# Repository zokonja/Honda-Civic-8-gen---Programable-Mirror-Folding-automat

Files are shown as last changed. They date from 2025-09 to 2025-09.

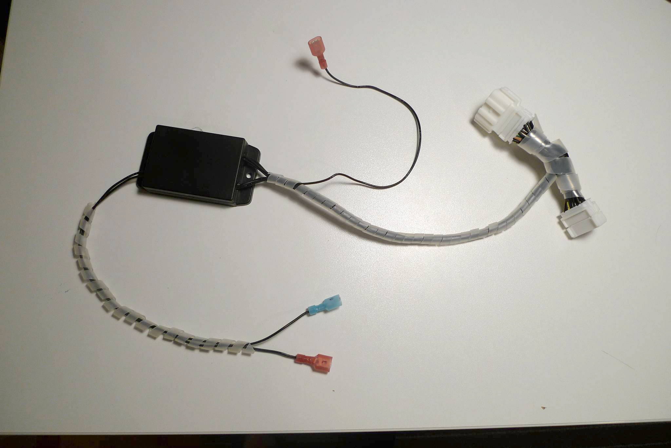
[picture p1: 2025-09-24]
Honda Civic 8 gen - Programable Mirror Folding automat/Pictures/P1070789.JPG

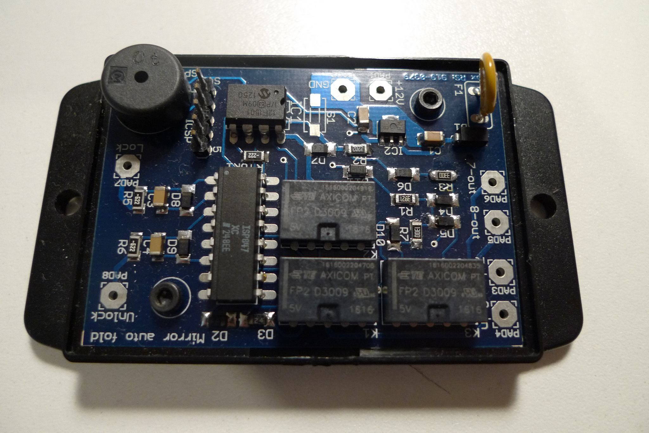
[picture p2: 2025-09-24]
Honda Civic 8 gen - Programable Mirror Folding automat/Pictures/P1070769.JPG

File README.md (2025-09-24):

Custom designed automat for Honda Civic 8gen for automatic mirrors fold/unfold.
Automat is programable and can be set to 5 different programs (behaviour actions).
Inside is complete device schematic (based on Microchip PIC 12F1501 micro) and firmware written in assembler and compiled HEX file for 12F1501.
Installation and demonstration video: https://youtu.be/eVyPs17ZJMc

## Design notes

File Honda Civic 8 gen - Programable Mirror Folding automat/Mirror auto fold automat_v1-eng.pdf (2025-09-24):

### Programable mirror folding automat (Civic 8th gen)

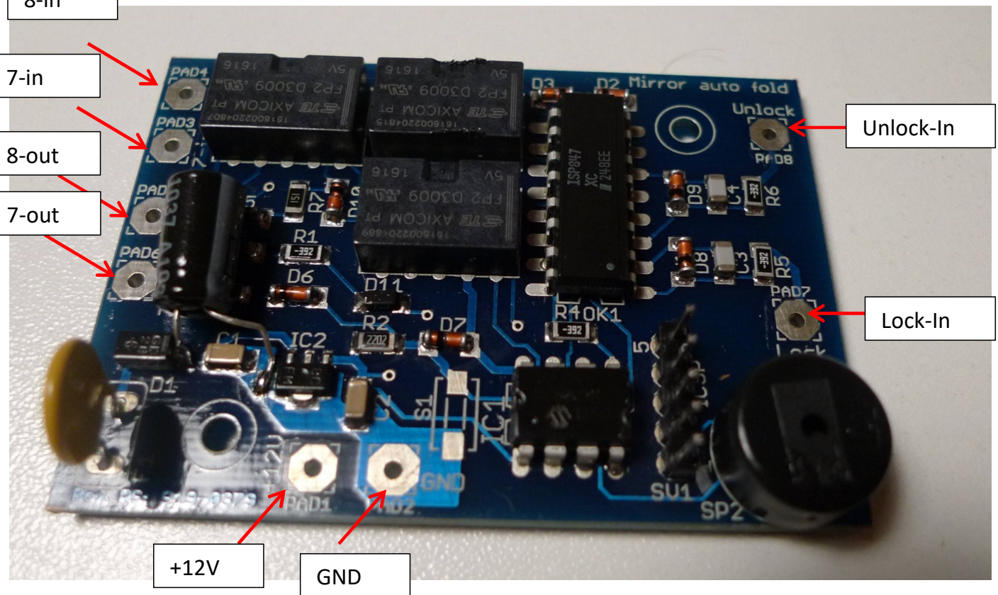
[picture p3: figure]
8-out; 7-out; GND; Unlock-In; Lock-In

Pin | Function | Connected to ...
GND | Ground (-) | Y connector
+12V | Power supply 12V (permanent) | 12V power supply on the window connector
8 - inch | Pin 8 from the female connector – signal from the mirror switch. If 12V appears at that input, it signals that the contact is ON. The same input detects whether the mirror switch is pressed. If the input is connected to ground (GND), the switch is pressed. | Y connector
7 - inch | Pin 7 from the female connector - signal from the mirror switch. If 12V appears at that input, it signals that the contact is ON. | Y connector
8 - out | Pin 8 from male connector, output to mirrors | Y connector
7 - out | Pin 7 from male connector, output to mirrors | Y connector
Lock-in | Lock signal input, 12V active | Central connector
Unlock - in | Unlock signal input, 12V active | Central connector

The Lock and Unlock signals are filtered from interference in the controller's SW, 80 ms debouncing time means that the signal must be active for a minimum of 80 ms without interruption in order to be processed.

The "8-in" mirror switch signal is filtered in the controller SW, 200 ms debouncing time means that the switch must spend a minimum of 200 ms in any state (down or up) to be processed correctly, otherwise it is ignored (noisy protection or bad switching action from switch itself).

8-in

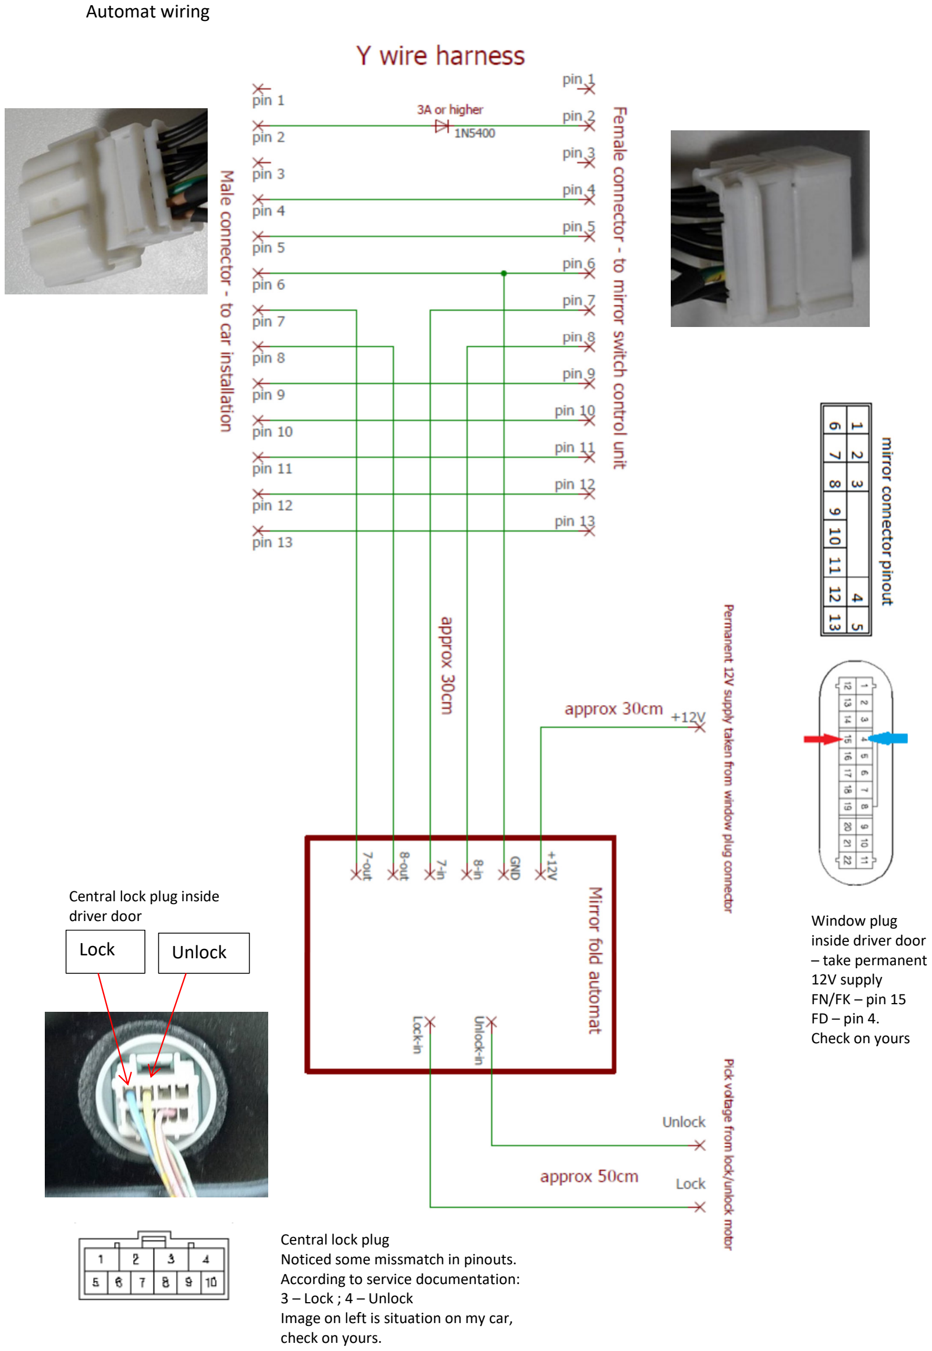
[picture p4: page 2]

Automat wiring

Lock | Unlock

Window plug
inside driver door
– take permanent
12V supply
FN/FK – pin 15
FD – pin 4.
Check on yours

Central lock plug inside
driver door

Central lock plug
Noticed some missmatch in pinouts. According to service documentation: 3 – Lock ; 4 – Unlock
Image on left is situation on my car, check on yours.

Function testing on table

1. - connect 12V power supply (+12V and GND), do not connect anything to the other inputs, the controller makes short sounds, the number corresponds to the saved program.
2. – supply 12V to the Lock or Unlock input (1x or 2x), according to the set program, the controller energise relays and performs the action of unfolding or folding the mirrors, the voltage is present at the "7-out" and "8-out" outputs and lasts for 10 seconds.
The output voltage is set according to this scheme depending on the action
| 7-out | 8-out
Fold | + 12V | GND
Unfold | GND | +12V

Actions depending on the program

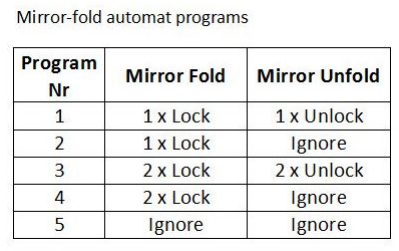
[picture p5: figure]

If a buzzer sounds instead of the desired action, it means that one of the conditions is not met:

### 1 x buzzer - the selected program does not support this action, the command is ignored

(program 2, 4 or 5)
2 x buzzing - mirror switch in down position ("8-in" connected to ground), command ignored.

### 3. Contact simulation, connect "7-in" or "8-in" to +12V

4. Simulation of the mirror switch in the folded position (down position), connect the "8-in" to ground

Changing the program
- Turn on and off the ignition (connect the "7-in" or "8-in" to 12V and then disconnect the 12V)
- Within 3 seconds, start pressing the mirror button ("8-in" connect to ground and disconnect), after the third press, the buzzer will sound a two-tone sound TU-TII
- After that, the buzzer counts down the number of times according to the currently recorded program number and ends with TU-TII.
- Start pressing the mirror button ("8-in" connect to ground and disconnect) as many times as you want to select a new program
- The buzzer sounds TU-TII and then repeats the number of the new program that was recorded and ends with TU-TII.
Notes:
The Lock/Unlock and “8-in” inputs are debounce filtered, 80 ms (Lock/Unlock) and 200 ms “8-in”. This means that the signal at these inputs must be high without interruption for a minimum of that time in order to be processed, otherwise it is ignored (it is considered interference). Pay special attention to this when simulating the rearview mirror switch, that the contact (connection to ground) is permanent for a minimum of 200ms.

If the buzzer sounds with the tone TI-TUU (higher then lower tone) when changing the program, this means that programming has been interrupted, too much time has passed since the moment when a new program should have been set (the rearview mirror button was not pressed / the "8-in" was not connected to ground) or the wrong program number has been set (button pressed more than 5 times => non-existent program).

PCB overview

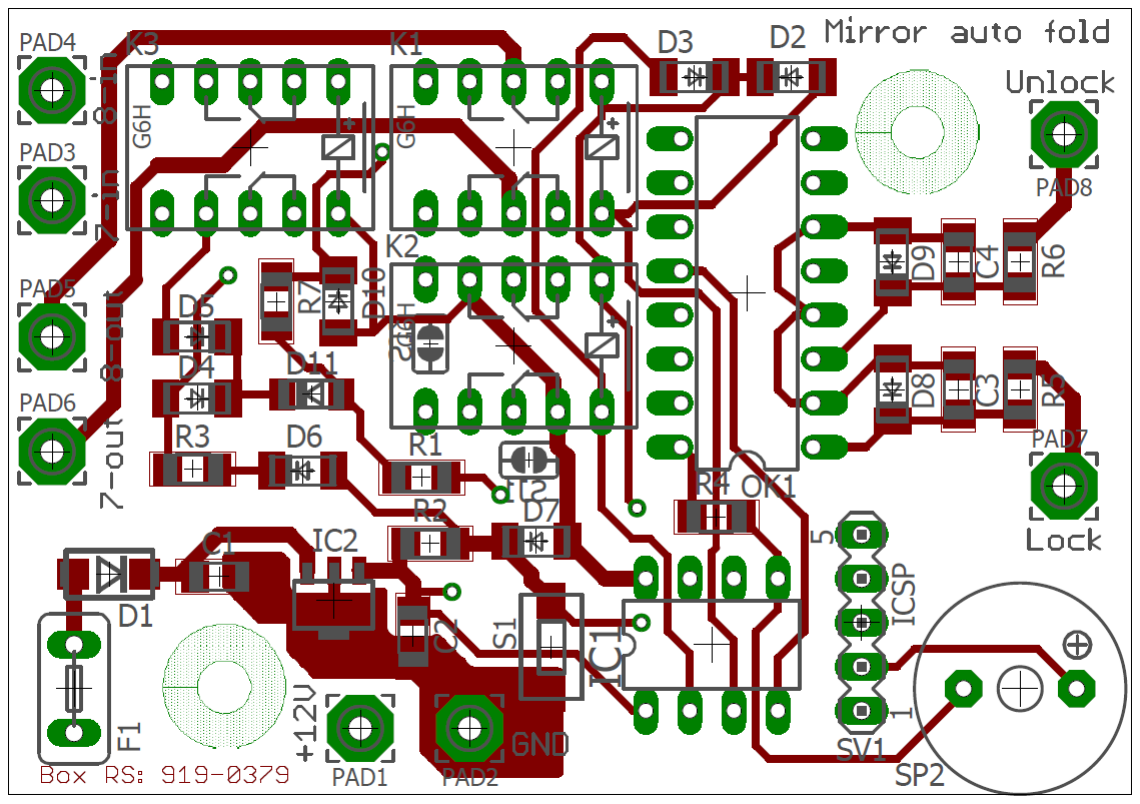
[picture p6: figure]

All SMD capacitors and resistors are 1206 (inch) size, capacitors minimum 25V.
Relays: TE FP2 or IM03TS (5V coil)
PCB is designed to fit in enclosure RS PRO : 919-0335 or 919-0379 (RS PRO ABS Enclosure, Flanged, Black Lid, 70 x 50 x 29mm)
Switch S1 is not needed, it can be used for settings programs during functionality test
For sound device (SP2) use piezo speaker, not buzzer!! Since controller modulate 2 tone sounds it must be piezo speaker.

Specials connectors for Y-wire harness (red circle) I could not found on internet, I bought some existing mirror module from internet (For civic 8 gen which I didn’t like how it functions) and took connectors from it to assemble my harness. Finding this connectors could be most challenging for you, but I don’t like to cut wires on existing installation so I get this connectors as I only could. Connectors in blue circles are standard wire terminals that can be hooked directly on wire without cutting (search Aliexpress for “T-type Wire Connector Quick Electrical Terminal Crimp“

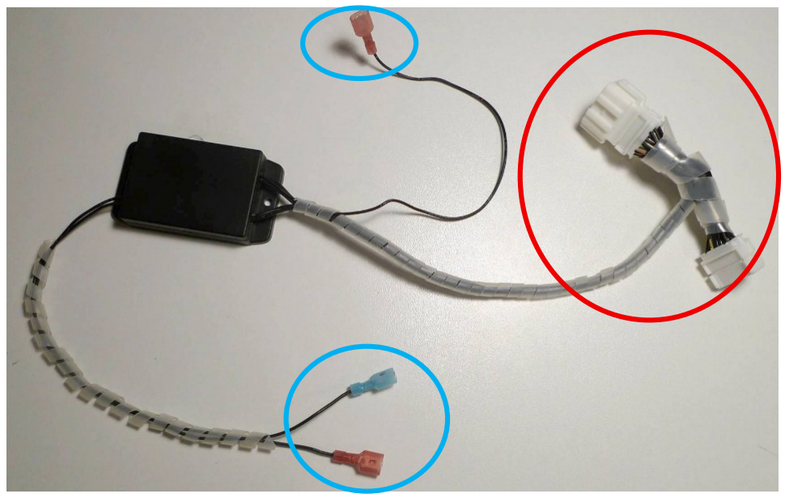
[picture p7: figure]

Demonstration video: https://youtu.be/eVyPs17ZJMc | (zokonjazokonja@gmail.com)

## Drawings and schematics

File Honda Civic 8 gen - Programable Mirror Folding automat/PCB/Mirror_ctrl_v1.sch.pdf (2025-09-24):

A

A

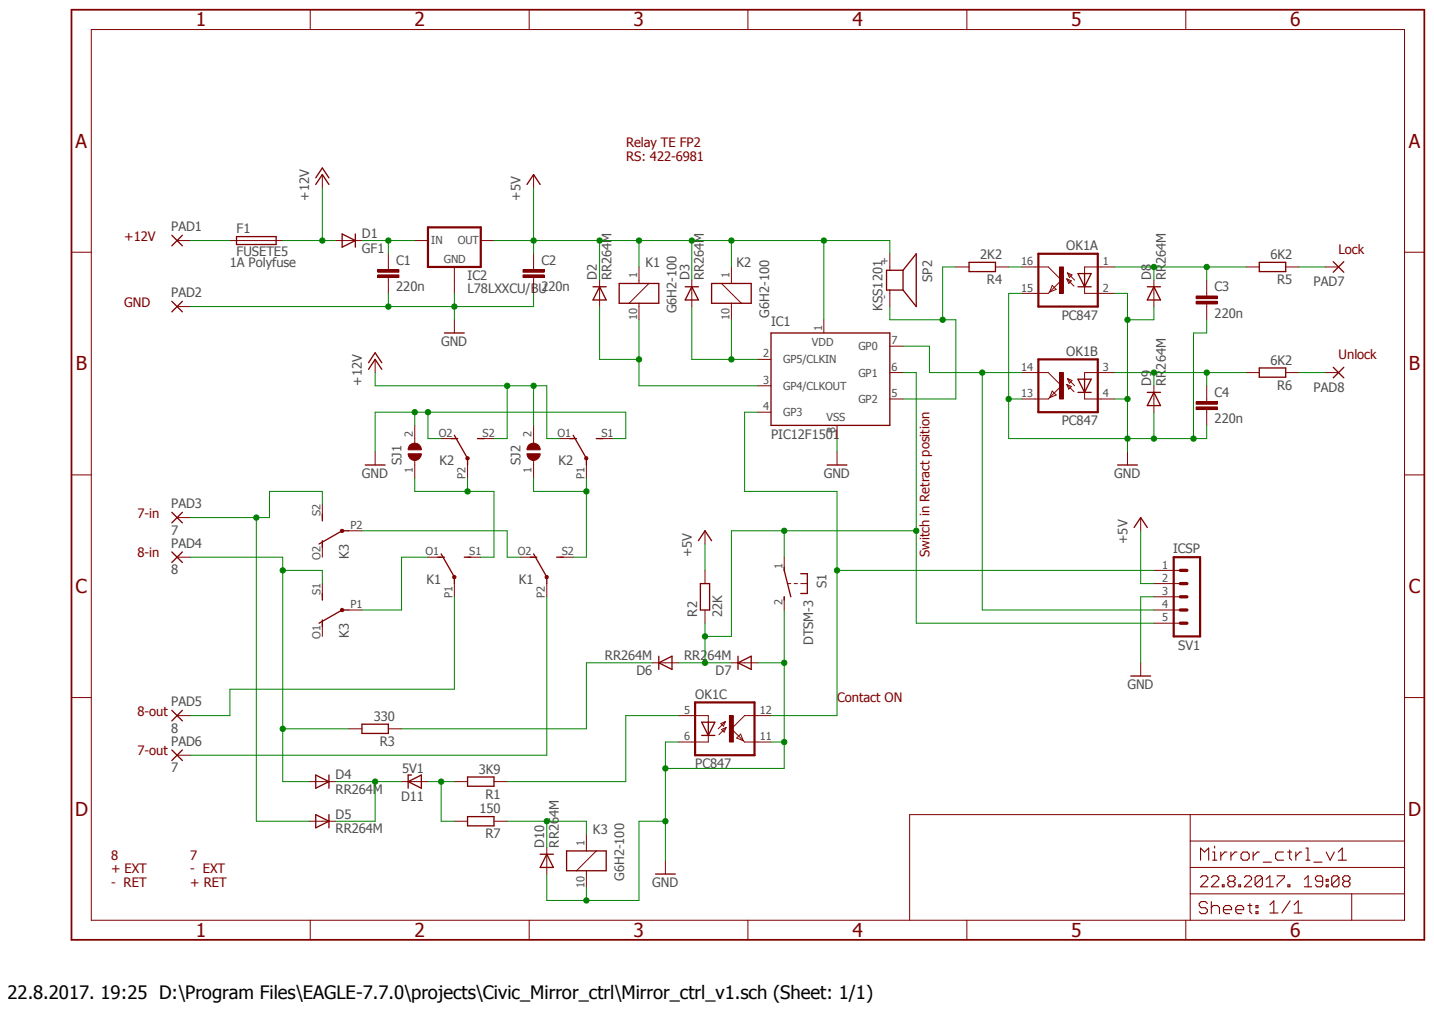
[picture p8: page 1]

Switch in Retract position

22.8.2017. 19:25 D:\Program Files\EAGLE-7.7.0\projects\Civic_Mirror_ctrl\Mirror_ctrl_v1.sch (Sheet: 1/1)

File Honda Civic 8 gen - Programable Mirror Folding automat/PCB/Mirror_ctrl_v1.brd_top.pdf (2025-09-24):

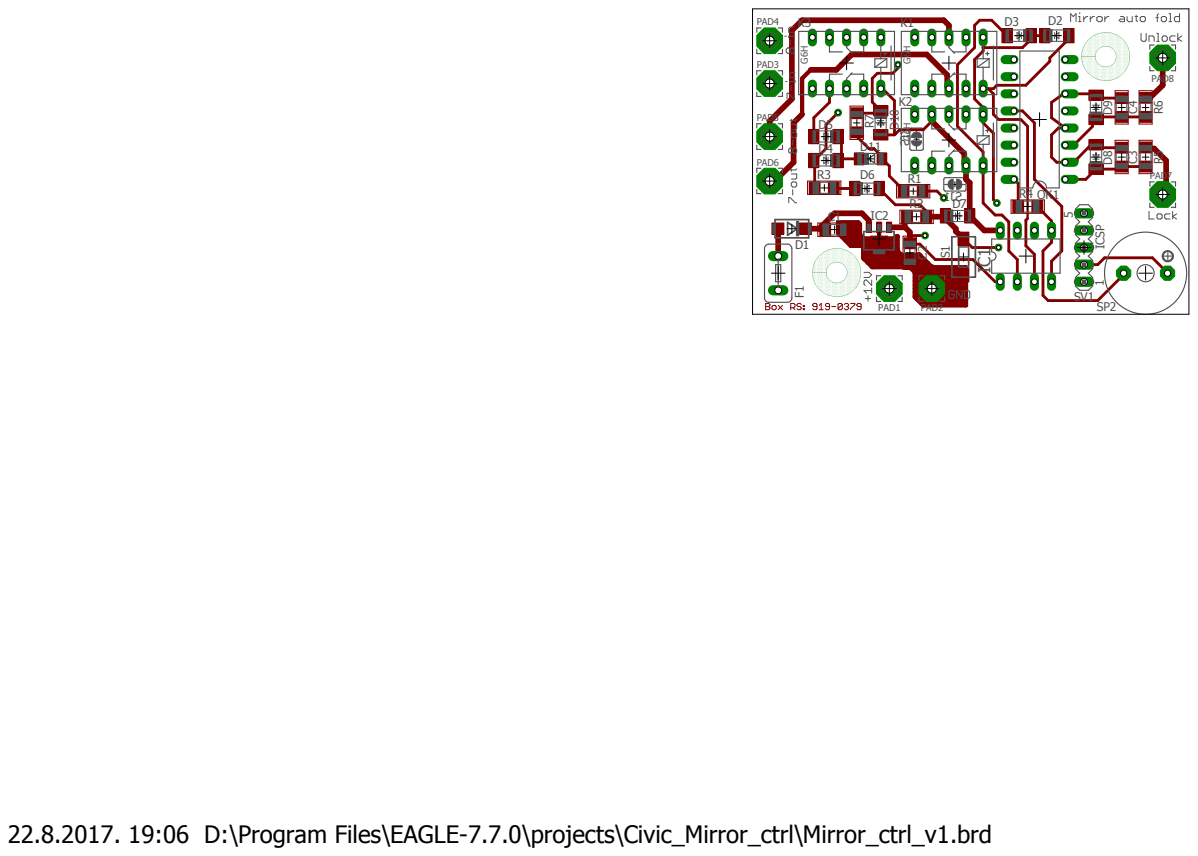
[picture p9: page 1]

22.8.2017. 19:06 D:\Program Files\EAGLE-7.7.0\projects\Civic_Mirror_ctrl\Mirror_ctrl_v1.brd

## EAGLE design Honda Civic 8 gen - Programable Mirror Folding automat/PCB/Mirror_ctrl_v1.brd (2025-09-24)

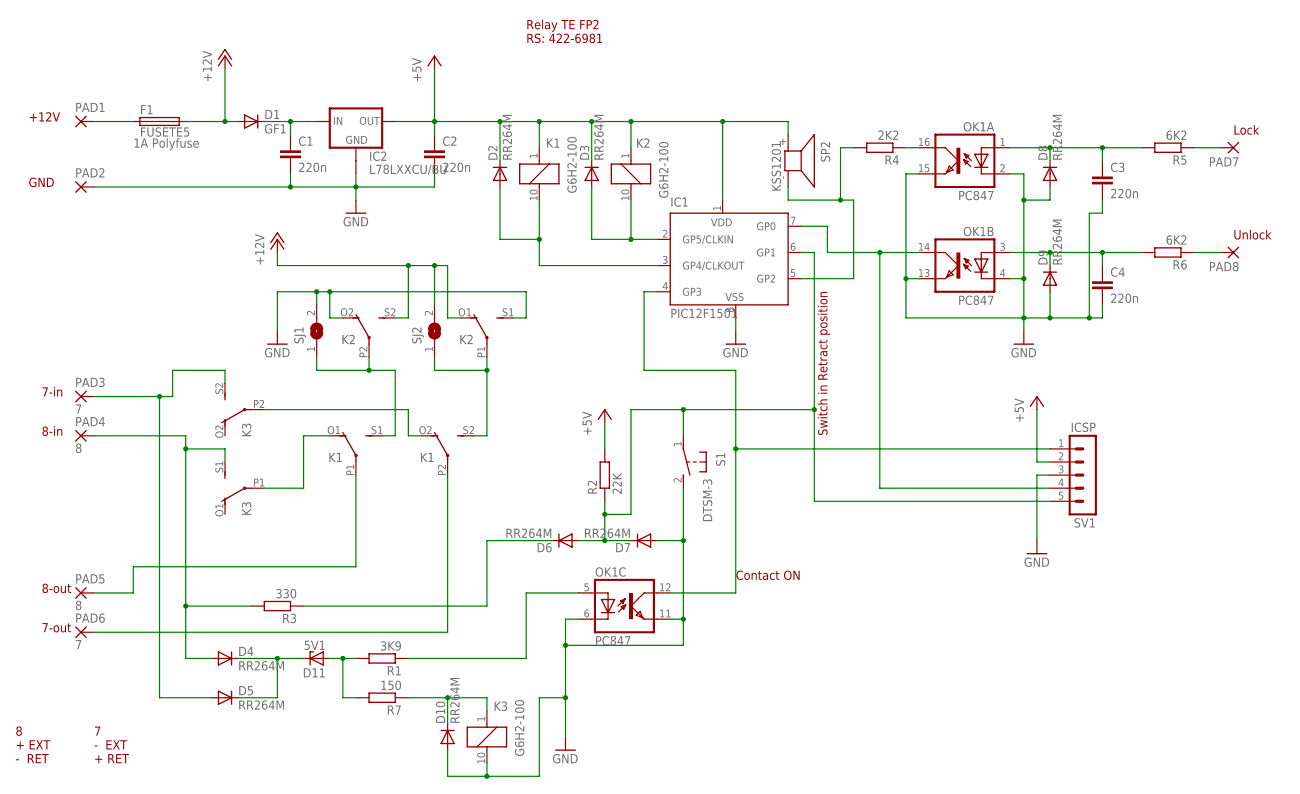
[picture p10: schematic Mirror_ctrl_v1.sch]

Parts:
C1, C2, C3, C4: 220n; C1206
D1: GF1; DO214BA
D2, D3, D4, D5, D6, D7, D8, D9, D10: RR264M; SOD-123_MINI-SMA
D11: 5V1; SOD80C
F1: FUSETE5; TE5
IC1: PIC12F1501; DIL8
IC2: L78LXXCU/BU; SOT89
K1, K2, K3: G6H2-100
OK1: PC847; DIL16
PAD1, PAD2, PAD7, PAD8: 3,81/1,4
PAD3, PAD6: 7; 3,81/1,4
PAD4, PAD5: 8; 3,81/1,4
R1: 3K9; R1206
R2: 22K; R1206
R3: 330; R1206
R4: 2K2; R1206
R5, R6: 6K2; R1206
R7: 150; R1206
S1: DTSM-3
SJ1, SJ2: SJ
SP2: KSS1201
SV1: ICSP; MA05-1

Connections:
+5V: C2.1, D2.C, D3.C, IC1.1 (VDD), IC2.1 (OUT), K1.1, K2.1, R2.2, SP2.+ (1), SV1.2
+12V: D1.A, F1.2, K2.O1 (O), K2.S2 (S), SJ2.2
GND: C1.2, C2.2, C3.2, C4.2, D7.A, D8.A, D9.A, D10.A, IC1.8 (VSS), IC2.4 (GND1), K2.O2 (O), K2.S1 (S), K3.10 (2), OK1.2 (C), OK1.4 (C), OK1.6 (C), OK1.11 (EMIT), OK1.13 (EMIT), OK1.15 (EMIT), PAD2.1, S1.2, SJ1.2, SV1.3
unnamed: D3.A, IC1.2 (GP5/CLKIN), K2.10 (2)
unnamed: C1.1, D1.C, IC2.3 (IN)
unnamed: F1.1, PAD1.1
unnamed: C3.1, D8.C, OK1.1 (A), R5.2
unnamed: D4.A, K3.S1 (S), PAD4.1, R3.2
unnamed: D5.A, K3.S2 (S), PAD3.1
unnamed: K1.P1, PAD5.1
unnamed: K1.P2, PAD6.1
unnamed: PAD7.1, R5.1
unnamed: D2.A, IC1.3 (GP4/CLKOUT), K1.10 (2)
unnamed: OK1.5 (A), R1.1
unnamed: D11.A, R1.2, R7.2
unnamed: K1.S1 (S), K2.P2, SJ1.1
unnamed: PAD8.1, R6.1
unnamed: K1.S2 (S), K2.P1, SJ2.1
unnamed: C4.1, D9.C, OK1.3 (A), R6.2
unnamed: IC1.4 (GP3), OK1.12 (COL), SV1.1
unnamed: IC1.7 (GP0), OK1.14 (COL), SV1.4
unnamed: OK1.16 (COL), R4.1
unnamed: D6.C, R3.1
unnamed: IC1.5 (GP2), R4.2, SP2.- (2)
unnamed: D6.A, D7.C, IC1.6 (GP1), R2.1, S1.1, SV1.5
unnamed: K1.O2 (O), K3.P2
unnamed: D10.C, K3.1, R7.1
unnamed: K1.O1 (O), K3.P1
unnamed: D4.C, D5.C, D11.C

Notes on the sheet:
+12V
GND
7-in
8-in
8-out
7-out
Lock
Unlock
Contact ON
1A Polyfuse
Switch in Retract position
Relay TE FP2 RS: 422-6981
8 + EXT - RET
7 - EXT + RET

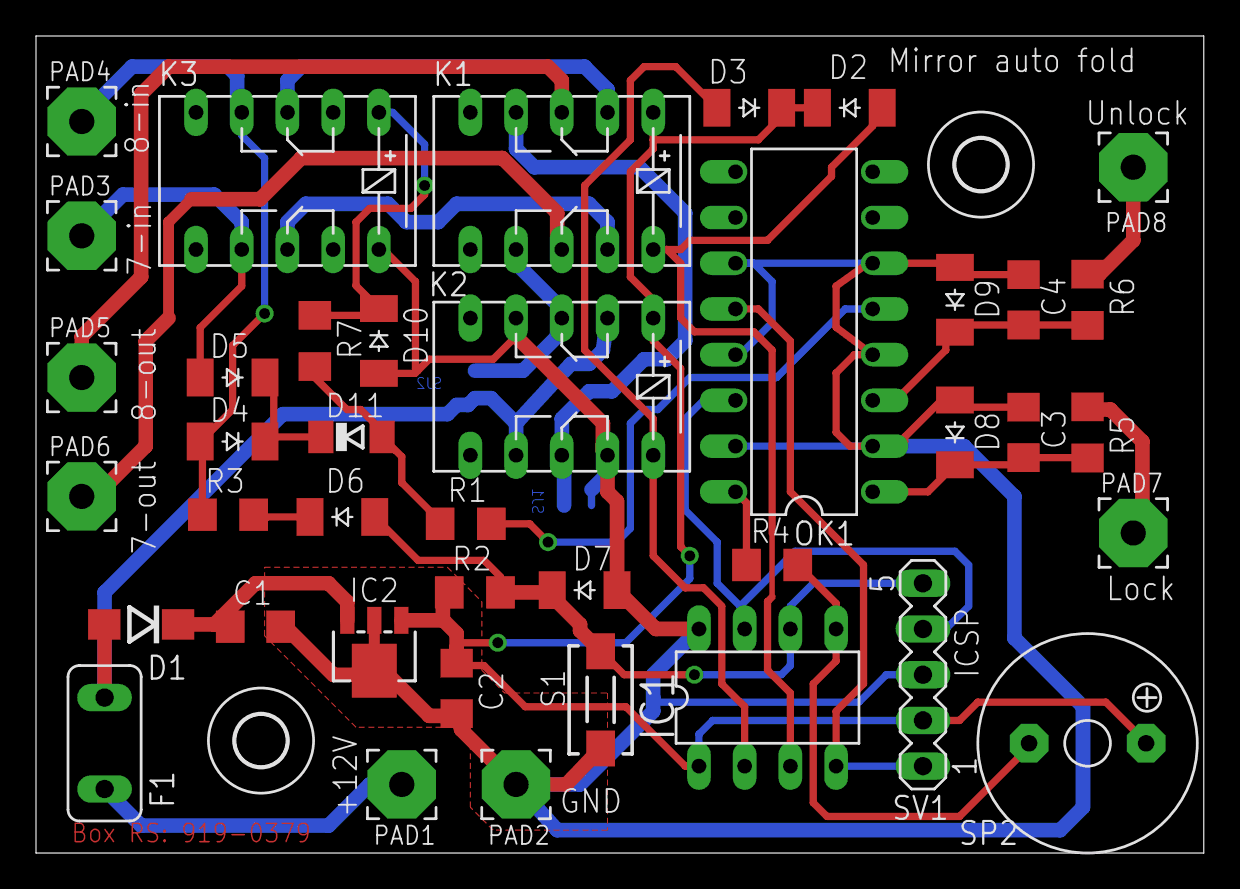
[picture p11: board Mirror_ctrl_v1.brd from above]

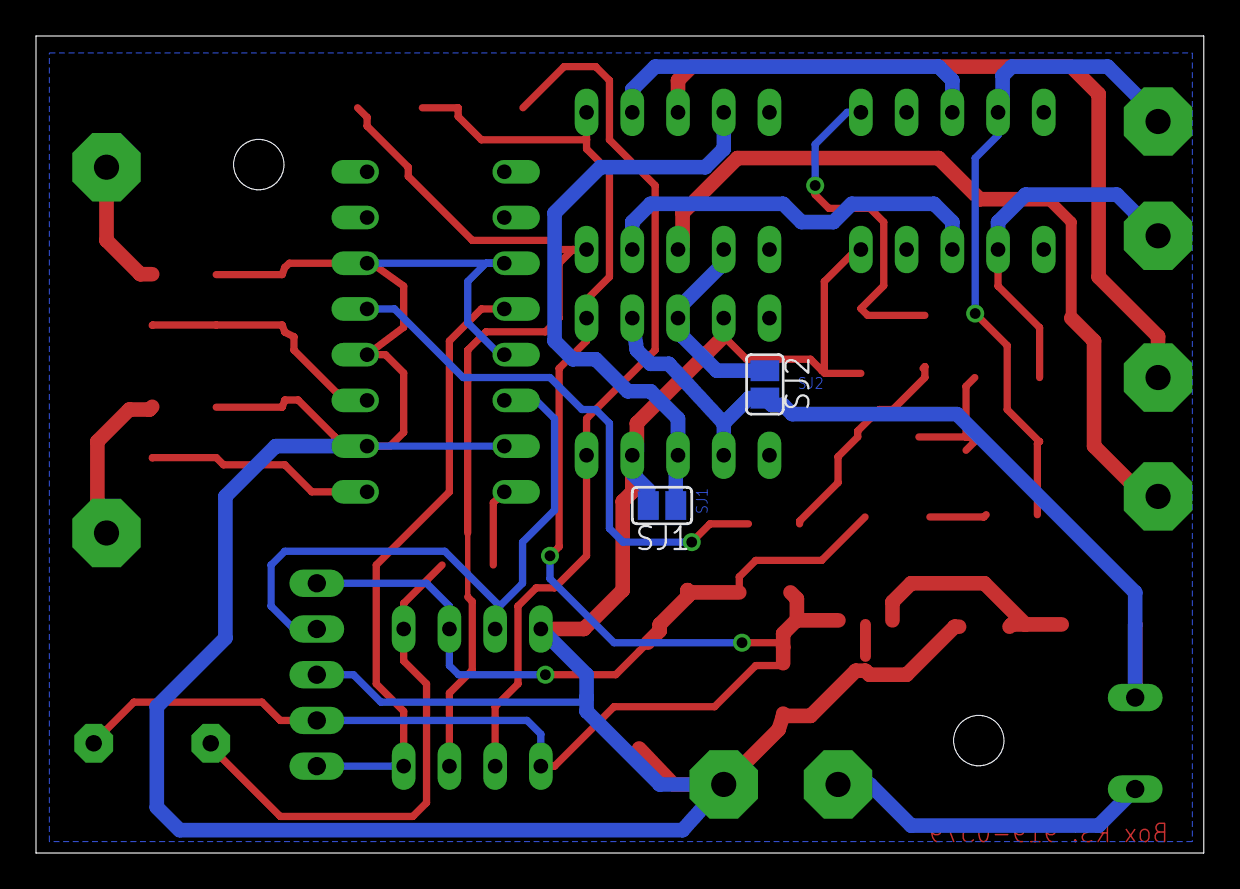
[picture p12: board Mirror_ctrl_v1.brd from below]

Board: 2 copper layers, 64.9 x 45.4 mm, 44 parts (2 on the bottom side), 29 nets.

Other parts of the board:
U$1, U$3: 2,8

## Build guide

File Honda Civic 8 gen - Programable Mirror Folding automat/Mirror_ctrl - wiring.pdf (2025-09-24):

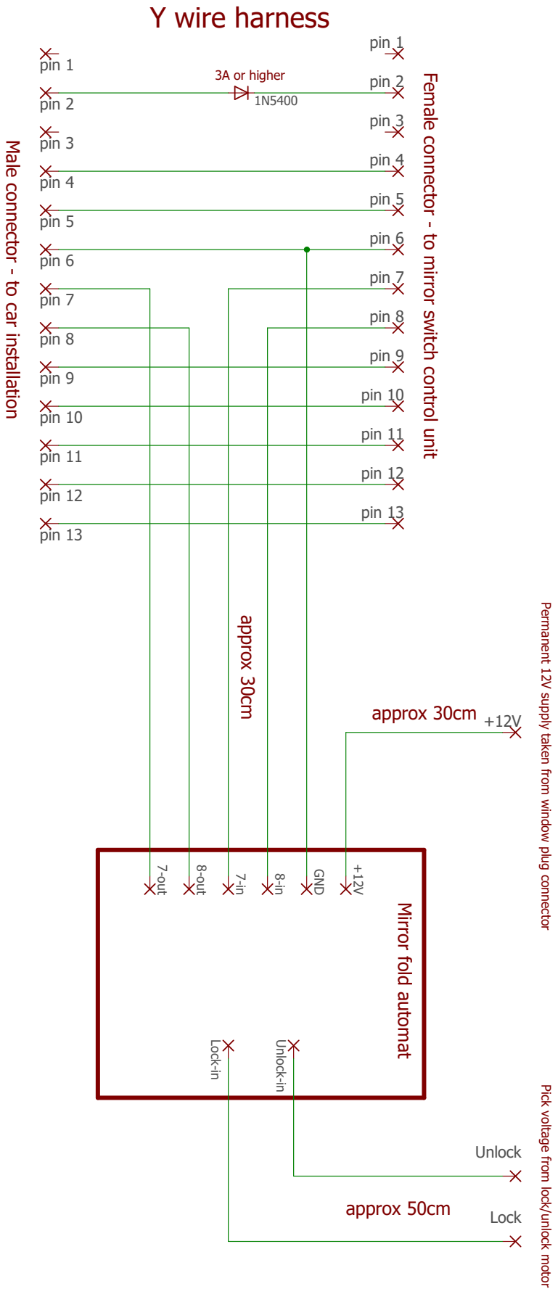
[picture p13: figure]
pin 1; pin 2; pin 3; pin 4; pin 5; pin 6; pin 7; pin 8; pin 9; pin 10; pin 11; pin 12; 7-out; 8-out; GND; Lock-in; Unlock-in; Unlock; Lock; pin 13; Mirror fold automat; approx 30cm; approx 50cm; 3A or higher; Male connector - to car installation; Y wire harness

19.9.2025. 21:39 C:\Users\Zoran_PC\Documents\eagle\Eagle 770 projects\Civic_Mirror_ctrl\Mirror_ctrl - wiring.sch (Sheet: 1/1)

Female connector - to mirror switch control unit

Pick voltage from lock/unlock motor Permanent 12V supply taken from window plug connector

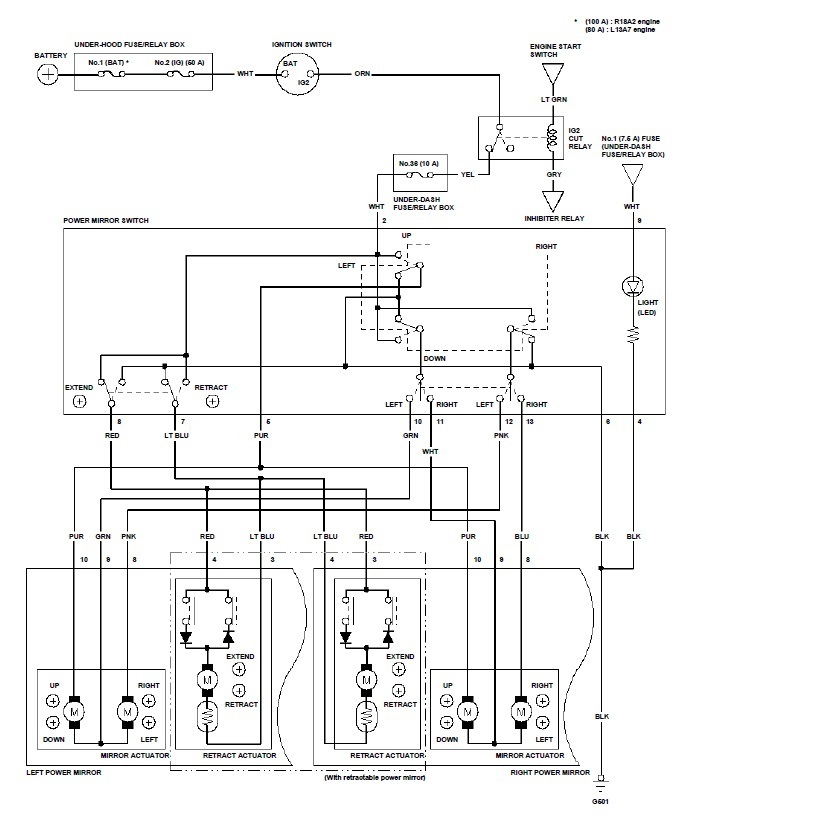
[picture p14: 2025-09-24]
Honda Civic 8 gen - Programable Mirror Folding automat/mirror schematic - from Civic service manual.jpg

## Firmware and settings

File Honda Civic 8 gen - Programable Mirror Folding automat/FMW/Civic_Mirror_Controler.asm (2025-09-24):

; ===========================================================================================================================
; Program koji upravlja sa modulom za kontrolu retrovizora preko daljinkog od otkljuèavanja i zakljuèavanja vrata
; dizajniran za Hondu Civic 8 gen, ali trebao bi moæi raditi na bilo kojem autu sliène konfiguracije
; (mehanièkog prekidaèa za položaj retrovizora i da ima SOD module u retrovizorima)
; Ver 2 - 17.07.2017
; Pojaèano debounce filtriranje, uveden RETRACT_DEBOUNCE_PAR
; Riješen bug kod dolaska napajanja da se releji ne aktiviraju na kratko
; Promijenjena frekvencija HI i LO tona, da se bolje èuje
; ===========================================================================================================================
	
	LIST P=12F1501, R=DEC
	#include "P12F1501.INC"


	__CONFIG _CONFIG1, _CLKOUTEN_OFF & _BOREN_NSLEEP & _CP_ON & _MCLRE_OFF & _PWRTE_ON & _WDTE_OFF & _FOSC_INTOSC
	__CONFIG _CONFIG2, _LVP_OFF & _BORV_LO & _STVREN_ON & _WRT_OFF 

; Internal oscilator 4MHz


;			Absolute definition variables

W_temp	equ	0x7F


	CBLOCK	0x20 		; rezerviranje mjesta u RAM-u

	MY_FLAGS_1
	MY_FLAGS_2
	MY_FLAGS_3
	RTC1_cnt
	RTC2_cnt
	RTC3_cnt
	RTC4_cnt
	RTC5_cnt
	RTC6_cnt
	MAIN_POINTER
	BUZZER_INDEX
	BEEP_COUNTER
	BEEP_cnt
	LOCK_cnt
	UNLOCK_cnt
	EXT_DURATION_cnt
	RET_EXT_DURATION_cnt
	PROG_WINDOW_cnt
	SWITCH_RETRACT_cnt
	UNLOCK_DEBOUNCE_filter
	RETRACT_DEBOUNCE_filter
	CONTACT_DEBOUNCE_filter
	LOCK_DEBOUNCE_filter
	BEEP_TONE_TIMER_cnt
	CONTACT_PAUSE_cnt
	AUTORESET_cnt
	SLEEP_cnt

	endc

	CBLOCK	0x7E	    ; dostupne varijable iz svih bankova

	DEVICE_MODE
	temp

	endc


;--------DEFINITIONS--------------------------

#define		RTC_1s						MY_FLAGS_1,0
#define		RTC_10ms					MY_FLAGS_1,1
#define		RTC_100ms					MY_FLAGS_1,2
#define		RTC_500ms					MY_FLAGS_1,3
#define		RTC_10s						MY_FLAGS_1,4
#define		TIME_ELAPSED					MY_FLAGS_1,5
#define		PWR_UP_flag					MY_FLAGS_1,6
	
#define		CONTACT_OFF_AC_flag				MY_FLAGS_2,0
#define		CONTACT_ON_flag					MY_FLAGS_2,1
#define		SW_RETRACT_ON_flag				MY_FLAGS_2,2
#define		LOCK_ON_flag					MY_FLAGS_2,3
#define		UNLOCK_ON_flag					MY_FLAGS_2,4
#define		SW_RETRACT_AC_flag				MY_FLAGS_2,5
#define		BUZZER_TU_TII_flag				MY_FLAGS_2,6
#define		BUZZER_TI_TUU_flag				MY_FLAGS_2,7
	
;-------------------- CONSTANTS ----------------------------------------


FALSE				EQU	0
TRUE				EQU	1
RET_EXT_DURATION_PAR		EQU	100	; x 100 ms   120
PROG_WINDOW_PAR			EQU	30	; x 100 ms , vremenski prozor za ulazak u mod programiranja
						; i timeout unutar moda programiranja
SWITCH_RETRACT_PAR		EQU	3
LOW_TONE_PAR			EQU	64
HIGH_TONE_PAR			EQU	59
SHORT_BEEP_TIMER_PAR		EQU	20	; x 10ms - bipanje, prvi ton
LONG_BEEP_TIMER_PAR		EQU	30	; x 10ms - bipanje, drugi ton
BEEP_PAUSE_TIMER_PAR		EQU	80	; x 10ms - pauza nakon bipanja
AUTORESET_PAR			EQU	30	; x 1s - autoreset LOCK i UNLOCK brojaca
SLEEP_PAR			EQU	18	; x10s - vrijeme za spavanje
RETRACT_DEBOUNCE_PAR		EQU	20	; x10ms - debounce filter za prekidac retrovizora
		

;-------------------- I/O Pins -----------------------------------------

#define		UNLOCK_IN			PORTA,0
#define		LOCK_IN				PORTA,2
#define		CONTACT_IN			PORTA,3
#define		SW_RETRACT_IN			PORTA,1
#define		BYPASS_OUT			PORTA,4
#define		EXT_RETRACT_OUT			PORTA,5				
				
;----------------------- MACROS -----------------------------------------
				
BANK_0	macro
	BANKSEL	PORTA
	endm
	
RELAY_RETRACT_POSITION	macro
	bsf	EXT_RETRACT_OUT
	endm
	
RELAY_EXTEND_POSITION	macro
	bcf	EXT_RETRACT_OUT
	endm
	
RELAY_BYPASS_ON	    macro
	bcf	BYPASS_OUT
	endm
	
RELAY_BYPASS_OFF    macro
	bsf	BYPASS_OUT
	endm
	
				
;===============================================================================



	ORG	0

	GOTO	Main
	
	ORG	4	; Interrupt vektor

	GOTO	Interrupt
	

;====================================================================
;			Main Program
;====================================================================
Main
	
	CLRF	INTCON  		; onemoguæi sve interrupte, obrisi sve flagove
								; od moguæih interrupta
	BANKSEL	PIR1
	CLRF	PIR1			; Obrisi sve flagove od perifernih interrupta
	CLRF	PIR2
		
	CLRF	T1CON
	movlw	B'00000001'			; TMR2 Postscale 1:1, TMR2 OFF (za sada), Prescale 1:4
	movwf	T2CON
	movlw	h'FF'
	movwf	PR2
		
        BANKSEL PORTA
        CLRF    PORTA		;Init PORTA
        BANKSEL LATA		;Data Latch
	movlw	B'00110000'	;ugasi releje BYPASS i RETRACT preko LATA registara
        movwf   LATA
        BANKSEL ANSELA
        CLRF    ANSELA		;digital I/O
	
	    ;bank 1 -------------------------------
	BANKSEL	TRISA
	MOVLW	B'11001111'		; PORTA 4 i 5 su izlazi, ostalo ulazi
	MOVWF	TRISA

	MOVLW	B'00000001'		; PORT_B pull-ups omoguæeni, prescaler TMR0 - 1:4
	MOVWF	OPTION_REG	

	movlw	B'01101010'		; Internal Oscilator, 4 MHZ, 
	movwf	OSCCON						

	CLRF	PIE1
	bsf	PIE1,TMR2IE		; omoguci TMR2 prekid			
	CLRF	PIE2	

		; bank 4 -----------------------------------
	BANKSEL	WPUA
	movlw	B'00001101'
	movwf	WPUA		; ukljuèi pull-up na PORTA 0, 2 i 3
	
		; bank 12 ----------------------------------	

	BANKSEL	PWM1CON
	clrf	PWM1CON
	


		; bank 0 ----------------------------------
	
	BANKSEL	IOCAP
	movlw	B'00001101'
	movwf	IOCAP	    ; omoguæi unterrupt na rastuci brid na PORTA 0, 2 i 3 pinu 
	movwf	IOCAN	    ; omoguæi unterrupt na padajuci brid na PORTA 0, 2 i 3 pinu
;	BANKSEL	VREGCON
;	bcf	VREGCON,VREGPM	    ; omoguci Low power sleep down mode
		
	BANKSEL	PORTA
	RELAY_BYPASS_OFF
	RELAY_RETRACT_POSITION	

	movlw	h'20'		; delete RAM from h'20' to h'7F' 
	movwf	FSR0L
	clrf	FSR0H
Loop
	clrf	INDF0
	movf	FSR0L,W
	sublw	h'7F'
	btfsc	STATUS,Z
	goto	Finish_Loop
	incf	FSR0L,F
	goto	Loop
Finish_Loop
	
;----------------------------------------------------------------------------------------
	bcf	INTCON,TMR0IF
	bsf	INTCON,TMR0IE	; omoguci TMR0 prekid
	bsf	INTCON,IOCIE	; omoguci IOCIE prekid (prekid kod promjene stanja bilo kojeg pina
	clrf	TMR0
	bsf	INTCON,GIE


	
	
;-----------------------------------------------------------------------------------------
;*****************************************************************************************
;/////////////////////////////////////////////////////////////////////////////////////////
; 
; MAIN LOOP IS HERE
;
;/////////////////////////////////////////////////////////////////////////////////////////
;*****************************************************************************************
;-----------------------------------------------------------------------------------------

DUTY_LOOP
	CALL	RTC
	CALL	INPUT_HANDLER
	CALL	MAIN_HANDLER
	CALL	BUZZER_HANDLER
	CALL	WATCHDOG_MONITOR
		
WAIT_TO_TIME_ELAPSE

	BTFSS	TIME_ELAPSED
	GOTO	WAIT_TO_TIME_ELAPSE
	BCF	TIME_ELAPSED
		
	GOTO	DUTY_LOOP

;===================================================================
;			Interrupt rutina
;===================================================================
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
